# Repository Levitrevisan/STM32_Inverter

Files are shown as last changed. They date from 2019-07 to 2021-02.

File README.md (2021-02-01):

# STM32 Inverter
## Introduction:

University project: Simple micro-inverter using a STM32F103C8.

## Objectives

Generate 3 phase signal through SPWM with 120 degrees of phase diffence. The frequency, phase and amplitude should be controlled through digital buttons.

## Project Roadmap

*  [OK] Be able to generate 6 PWM pulses with different duty cycles
*  [OK] Be able to control duty cycles inside timmed interruption routines
*  [OK] Guarantee that interruption have the timer and counter well adjusted to required time.
*  [OK] Be able to generate 3 SPWM waves with 120 between them
*  [OK] Guarantee that SPWM generated have 120 degrees between them
*  [OK] Control SPWM Amplitude
*  [OK] Implement GPIO input interruption
*  [--] Read Zero Cross signal
*  [OK] Control phase based on Zero Cross signal

## Reference

*  https://www.infineon.com/dgdl/Infineon-IM393-S6E-DS-v02_00-EN.pdf?fileId=5546d462696dbf1201699a9d912478e4 - INFINEON CIPOS datasheet
*  https://www.infineon.com/dgdl/Infineon-AN2016-11_CIPOS_Mini_Inverter_module_reference_board_type1_for_1-shunt_resistor-AN-v01_11-EN.pdf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 - Evaluation board manual (used for "benchmarking" propuses)
*  https://www.st.com/content/ccc/resource/technical/document/reference_manual/59/b9/ba/7f/11/af/43/d5/CD00171190.pdf/files/CD00171190.pdf/jcr:content/translations/en.C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 - STM32 reference manual

## How to use MatLab script to generate SPWM values

The matlab script is used to generate the senoid values that are used as reference for the SPWM generation. You should se the parameters

```
  max_pwm_value = 3550;
  min_pwm_value = 0;
  frequency = 60;
  number_of_points_in_one_cycle = 60;
```

The script will return the int array to be pasted into the MCU code like this:

```
  {1775 ,1961 ,2144 ,2324 ,2497 ,2663 ,2818 ,2963 ,3094 ,3211 ,3312 ,3397 ,3463 ,3511 ,3540 ,3550 ,3540 ,3511 ,3463 ,3397 ,3312 ,3211 ,3094 ,2963 ,2818 ,2663 ,2497 ,2324 ,2144 ,1961 ,1775 ,1589 ,1406 ,1226 ,1053 ,888 ,732 ,587 ,456 ,339 ,238 ,153 ,87 ,39 ,10 ,0 ,10 ,39 ,87 ,153 ,238 ,339 ,456 ,587 ,732 ,887 ,1053 ,1226 ,1406 ,1589 ,}
```
  
It will also return the interuption period in nanoseconds used to control the timed interruption that will update the PWM values to generate the senoid. Lastly, it will show us the stem plot of those points.

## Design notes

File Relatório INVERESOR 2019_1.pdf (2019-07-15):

UNIVERSIDADE FEDERAL DO RIO GRANDE DO SUL- UFRGS ESCOLA DE ENGENHARIA - DEPARTAMENTO DE ENGENHARIA ELÉTRICA
APLICAÇÕES INDUSTRIAIS DA ELETRÔNICA

### Levi Trevisan Gustavo C. Casara Pedro Henrique Dal Pizzol

### Projeto Final da Disciplina de Aplicações Industriais da Eletrônica:

### Implementação de um inversor trifásico para adaptação da geração

fotovoltaica à rede.

Porto Alegre, 2019

Resumo

O projeto desenvolvido teve como objetivo implementar um inversor trifásico que permite que a energia gerada a partir de uma planta solar (tensão DC) possa ser injetada na rede.
A partir de uma série de PWMs modulados senoidalmente, conseguimos utilizar o chip IM393-S6E da INFINEON de maneira semelhante a um driver, usando como fonte a tensão DC de alta potência.
O projeto é separado entre parte de controle e parte de potência, elas têm isolamento galvânico entre si a partir de optoacopladores, em momento nenhum o nível de 3.3V do microprocessador estará exposto diretamente a parte de potência.
Utilizando um filtro do tipo passa-baixa na saída trifásica do projeto, pode-se observar uma saída trifásica com três senóides defasadas em 120º. Também foi projetado um filtro LCL para ser utilizado após o inversor.

1- Alimentações

1.1 - Microprocessador

O microprocessador utilizado foi o BluePill STM32. Nele há um regulador 3.3V de forma que qualquer alimentação entre 5V e 3.3V é suficiente para utilizá-lo.
Foi escolhida então uma fonte comum de celular 5V e 1A, pois já é compatível com a entrada USB mostrada na Figura 1

Figura 1 - BluePill STM32

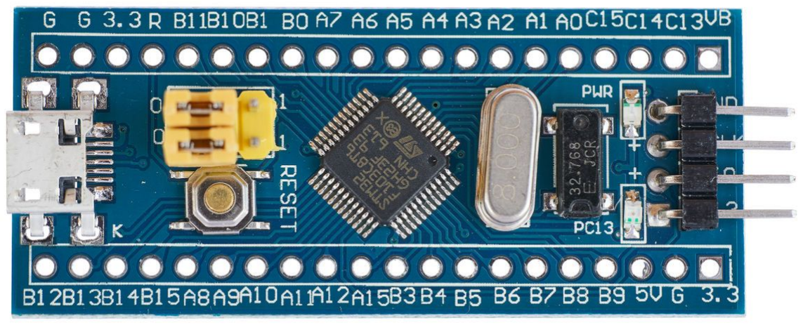
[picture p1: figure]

1.2 - IM393-S6E INFINEON

Para a alimentação do chip da INFINEON foi utilizada uma fonte de 15V 1,6A, que será conectada na rede para alimentar o chip e o regulador de 3.3V que será abordado a seguir.

### 1.3 Regulador 3.3V (parte de Potência)

Para alimentar o “secundário” dos optoacopladores com uma fonte isolada da parte de controle, aproveitamos os 15V que alimentam o INFINEON. A partir de um regulador LM317 ajustável, utilizamos um trimpot para ajuste fino da tensão que deve ser 3.3V.

Figura 2 - Esquemático do regulador de tensão de 3.3V

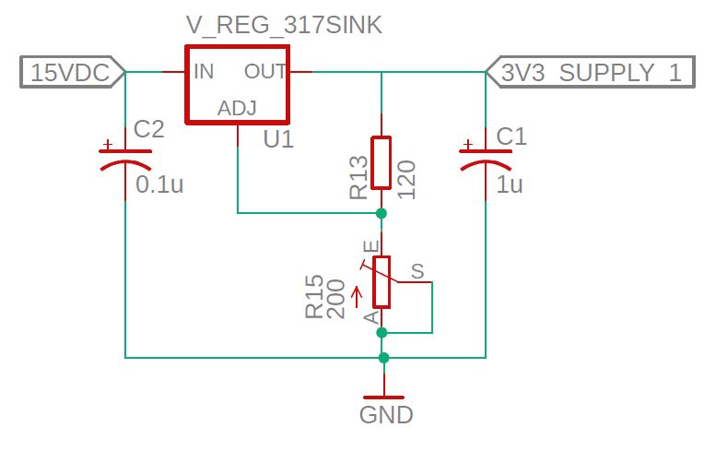
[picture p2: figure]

2- Controle

O controle da amplitude e da frequência do sinal de saída do inversor são feitos através de sinais PWM. Controlando a largura de cada pulso conseguimos, em média, diferentes níveis de tensão, da mesma forma, variando a média do sinal varia-se a frequência.
Para gerar os sinais PWM, que controlam cada um dos seis semi-ciclos (um semi-ciclo positivo e negativo para cada uma das três fases) foram utilizadas as portas PWM do microprocessador BluePill STM32, seus timers e funções de interrupção.
Foi definido que o sinal teria sessenta diferentes níveis de tensão, níveis estes, que seriam aplicados em sequência na saída, gerando uma senóide com “degraus”.
Para atender esta definição as interrupções foram definidas para ocorrerem a cada 277,77778µs e, assim, atualizar o valor do PWM para o valor seguinte.
Para o microprocessador utilizado temos que o valor máximo do sinal PWM é de 3550, para este valor o nível lógico da saída fica alto por do 100% do duty cicle. E para o valor zero o nível lógico fica baixo para todo o duty cicle.
Dividindo um período da senóide em 60 amostras, foi feito um vetor que apresenta os valores que devem ser utilizados para controlar o duty cicle do PWM.

senoid_pwm = [1775 ,1961 ,2144 ,2324 ,2497 ,2663 ,2818 ,2963 ,3094 ,3211 ,3312 ,3397 ,3463 ,3511 ,3540 ,3550 ,3540 ,3511 ,3463 ,3397 ,3312 ,3211 ,3094 ,2963 ,2818 ,2663 ,2497 ,2324 ,2144 ,1961 ,1775 ,1589 ,1406 ,1226 ,1053 ,888 ,732 ,587 ,456 ,339 ,238 ,153 ,87 ,39 ,10 ,0 ,10 ,39 ,87 ,153 ,238 ,339 ,456 ,587 ,732 ,887 ,1053 ,1226 ,1406 ,1589]

Plotando o vetor acima obtemos o seguinte gráfico:

Figura 3 - Plot com os gráficos de valores utilizados na função PWM do microprocessador.

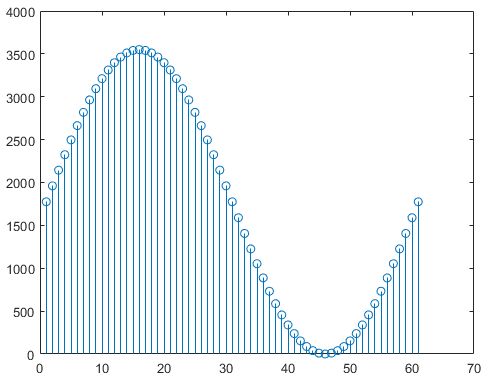
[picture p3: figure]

Como pode ser visto na Figura 2, a sequência dos valores do vetor senoid_pwm formam a senóide desejada e necessária para o projeto.
Para conseguir a defasagem de 120° entre as fases, a função PWM deve começar com primeira posição do vetor para a fase R, com a vigésima posição para a fase S e com a quadragésima posição para a fase T.

3- Isolamento Galvânico

O isolamento galvânico consiste em ter dois sistemas elétricos com terras diferentes que se comuniquem sem o fluxo de correntes indesejadas.
A isolação galvânica é importante para fins de segurança, de forma que um usuário que tenha acesso a botões ou ao microprocessador nunca entre em contato com a parte de potência e também é importante para fins de proteção, pois se houver algum problema com o circuito de potência o mesmo não afetará a parte de controle.
Para obter tal isolação, são utilizados optoacopladores. Foram feitos testes iniciais com os modelos 4N25 e PC817, porém nenhum deles demonstrou uma resposta satisfatória na frequência de 20kHz que o nosso PWM opera.
Optou-se então por utilizar um optoacoplador de alta velocidade. O modelo que encontramos em Porto Alegre para comprar foi 6N135. Quando este optoacoplador recebe o PWM na entrada do seu LED emissor interno diretamente do microprocessador ele inverte a saída, optamos por utilizar uma topologia alternativa mostrada na figura abaixo, nela temos dois ganhos, o microprocessador não precisa fornecer a corrente do PWM (um microprocessador sempre suporta receber mais corrente do que fornecer) e a saída do optoacoplador é a mesma que o PWM gerado no microprocessador.

Figura 4 - Topologia do 6N135

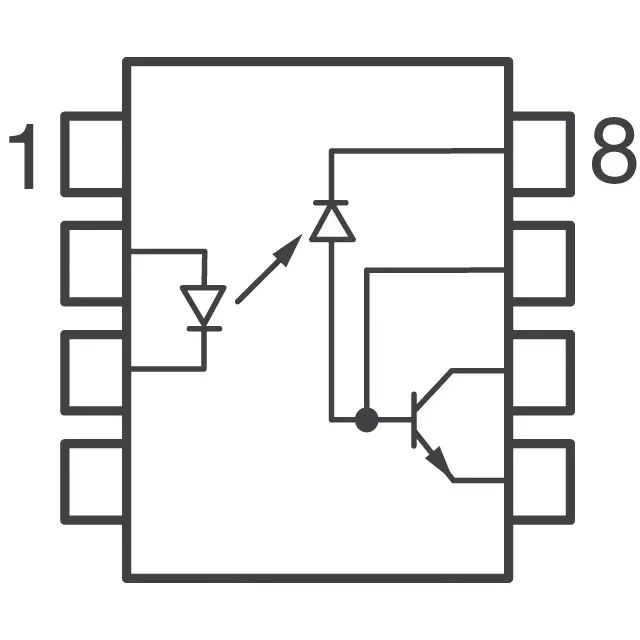
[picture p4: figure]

Figura 5 - Esquemático do isolamento galvânico através de optoacopladores

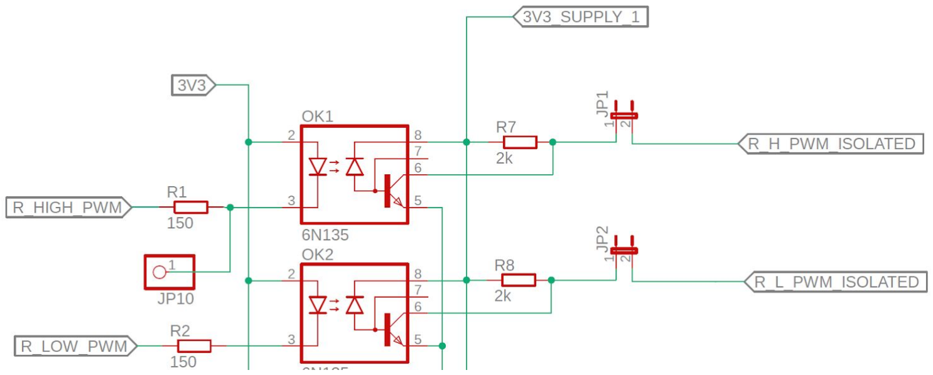
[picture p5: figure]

Podemos ver no lado “primário” do optoacoplador os PWMs do High Input e do Low Input do INFINEON. Os resistores R1 e R2 foram projetados para que haja uma corrente grande suficiente para que os LEDs emitam o sinal com a intensidade necessária.
Já no lado “secundário” há um resistor recomendado no datasheet do 6N135 e jumpers para fins de testes do circuito.

4- INFINEON

Caracterizamos como a parte de potência o nosso chip da INFINEON e o que envolve a tensão de 300V.
A tag “High DC in” é a entrada de 300V. Ela é conectada ao pino V+ do INFINEON. As alimentações de 15V vão nos pinos de VDD do chip. Adicionalmente, ambas referências (da fonte de 15V quando da fonte de 300V) irão no pino de COM do INFINEON.
Todos os pinos de Hin e Lin estão diretamente ligados nos “secundários” dos optoacopladores.
Também foram inseridos capacitores de bootstrap entre os pinos da saída Vs e os pinos de Vb, conforme indicado tanto no datasheet do chip quando em manuais de aplicação indicados pelo Professor.

Figura 6 - Esquemático utilizado para as ligações do INFINEON

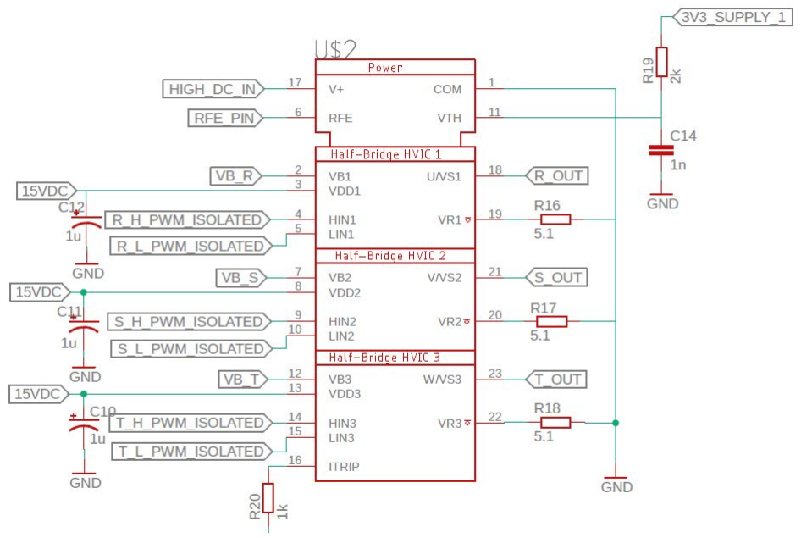
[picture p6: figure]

Figura 7 - Capacitores de BootsTrap entre a Vs e Vb

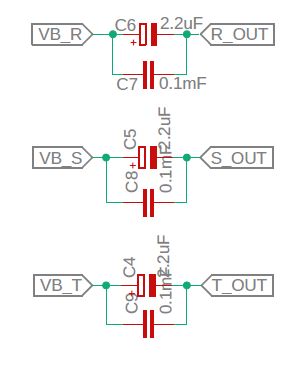
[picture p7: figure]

5- Detector de Passagem por zero

O detector de passagem por zero é o circuito capaz de detectar quando a tensão da rede AC passa de uma tensão negativa para positiva e vice-versa. Essa informação é útil em retificadores trifásicos grid-tie. Essa informação será utilizada pelo microprocessador para ajustar as fases deixando-as sincronizadas com a rede, ou levemente adiantada para que a energia flua dos painéis solares para a rede.
O led do optoacoplador conduzirá em apenas metade do período, o período positivo, assim obtém-se um sinal digital que indica quando a fase está no ciclo positivo e quando não está.

O resistor de 100KΩ limita a corrente evitando queimar o led. O diodo em paralelo com o optoacoplador serve para evitar a tensão reversa sobre o led.
Além do optoacoplador fornecer um sinal digital de interesse ele também serve de isolamento galvânico para o microprocessador.

Figura 8 - Esquemático do detector de zero.

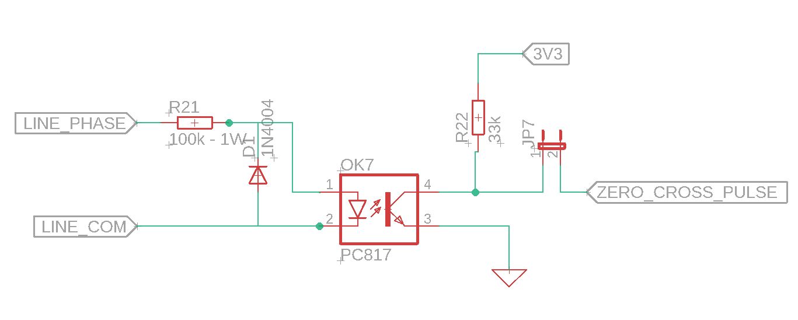
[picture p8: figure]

6- Filtro de saída

Para o filtro de saída de testes, foi utilizado um filtro RC passa-baixa. Utilizamos como frequência de corte 120Hz no teste.
O capacitor utilizado foi de 22uF e a resistência de 60Ω.

Figura 9 - Filtro passa-baixa RC.

Foi pedido também no projeto o dimensionamento de um filtro LCL. Foi utilizado como referência a dissertação de mestrado de Rômulo Diniz Araujo
(http://www.gpec.ufc.br/novasdissertacoes/13.pdf) e também as notas de aula do Prof. Heverton Augusto Pereira da UFV (http://www.gesep.ufv.br/wp-content/uploads/Aula_06-Conversores-cc_ca-Filtro-LCL.pdf).

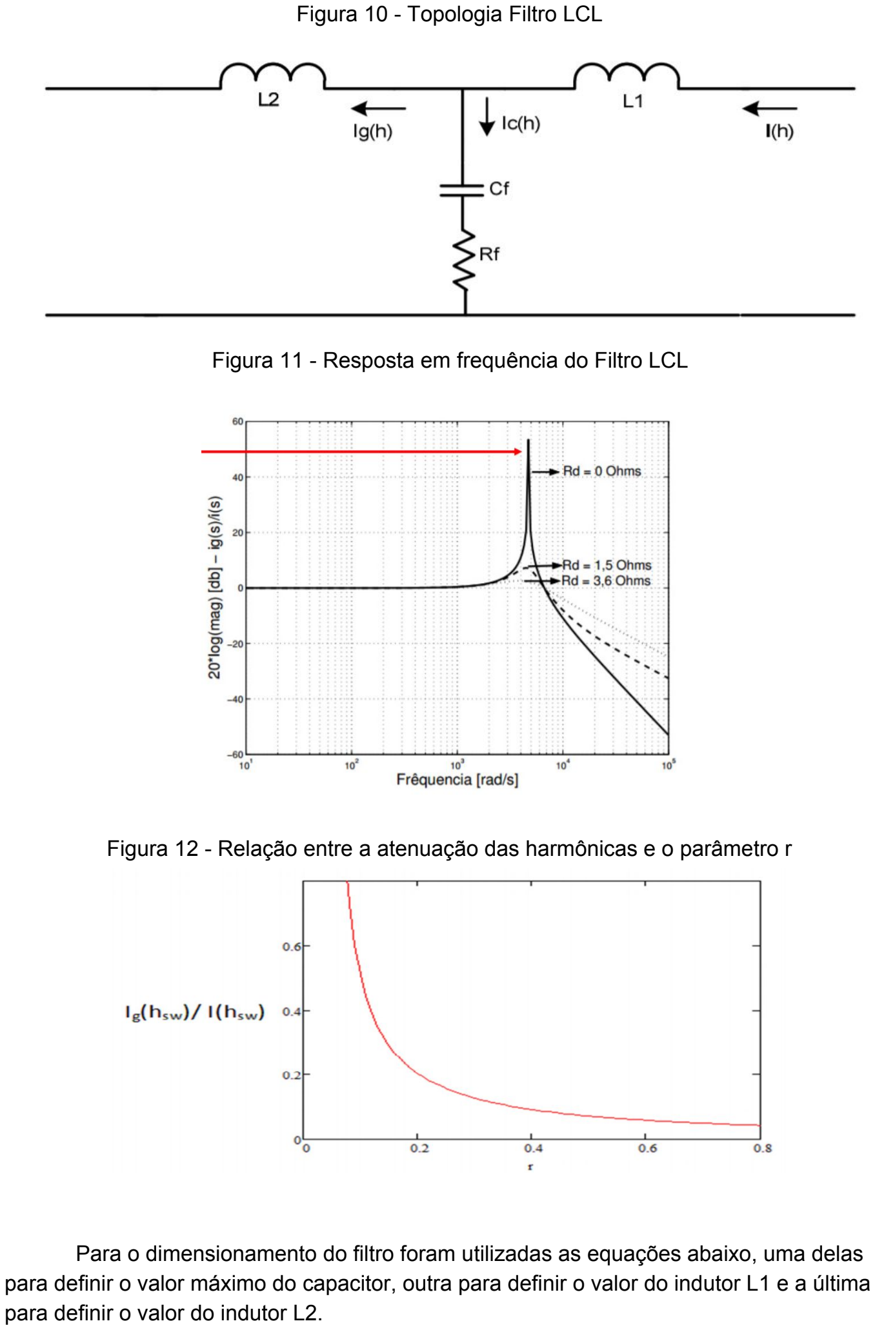
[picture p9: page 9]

Figura 10 - Topologia Filtro LCL

Figura 11 - Resposta em frequência do Filtro LCL

Figura 12 - Relação entre a atenuação das harmônicas e o parâmetro r

Para o dimensionamento do filtro foram utilizadas as equações abaixo, uma delas para definir o valor máximo do capacitor, outra para definir o valor do indutor L1 e a última para definir o valor do indutor L2.

O valor da capacitância máxima é representado na equação abaixo, ela é definida para que o fator de potência do filtro se mantenha alto, quanto maior a capacitância utilizada menor será o indutor necessário.
Foi utilizada como a nossa tensão de saída a tensão de linha da rede, a corrente máxima como 6A e frequência de chaveamento de 20kHz. No artigo, Rômulo Araujo utilizou como % de ripple na corrente 31% e o fator r como 20%, seguimos estas definições para o dimensionamento.

Os valores do dimensionamento estão no quadro abaixo.

L1 [mH] | L2 [mH] | Cf [nF] | Rf [Ω]
7,2 | 1,44 | 60 | 3,6

7 - Roteiro de Testes

Para um correto uso do inversor deve-se seguir os seguintes passos:

1. Ainda com o circuito desligado, deve-se retirar todos os 6 jumpers presentes na placa. Para impedir que qualquer qualquer sinal chegue em chip da INFINEON.
2. Alimentar o microprocessador com a fonte de 5V e verificar se ele está gerando os sinais PWM.
3. Alimentar o circuito com a fonte de 15V. Os 15V alimentam o regulador de tensão que alimenta os optoacopladores e demais circuitos relevantes.
4. Verificar se o regulador de tensão, agora alimentado com 15V, possui 3,3V na sua saída. Não sendo verdadeiro a tensão de saída pode ser regulada ajustando o trimpot.
5. Com o passo 4 atendido verifica-se as saídas dos optoacopladores. Neles devem ser observados os mesmos sinais PWM observados no passo 2.
6. Ligar uma das fases ao detector de passagem por zero. Verificar se existem pulsos na sua saída.
7. Verificar se o chip da INFINEON está alimentado com 15V nos pinos 3, 8 e 13.
8. Ligar a fonte de 300V.
9. Ler as saídas. O sinal deve ser parecido ao dos ítens 2 e 5.
10. Conectar o filtro a saída trifásica.
11. Ler as saídas depois de passarem pelo filtro.

Figura 13 - Saída do inversor após o filtro RC (fonte DC de 22,5V como alimentação)

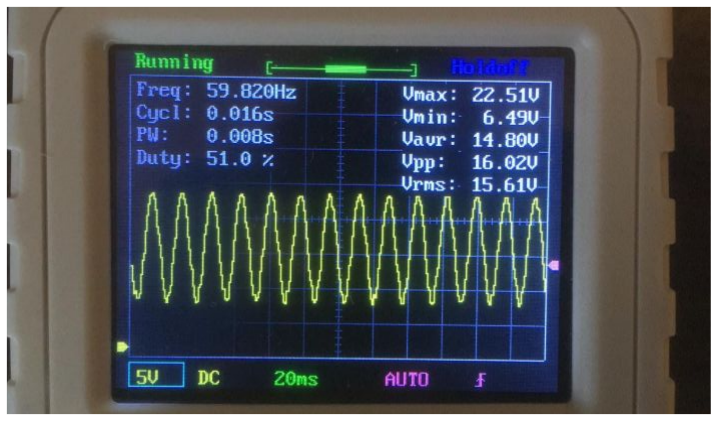
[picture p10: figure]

Figura 14- PWM na entrada do INFINEON (pelas limitações do osciloscópio só conseguimos congelar a parte de duty cycle baixo)

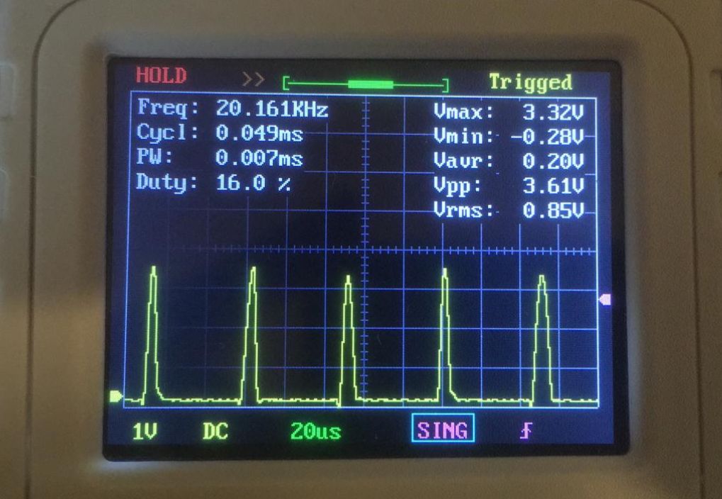
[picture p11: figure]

Figura 14- PWM na saída do INFINEON com 24V CC.

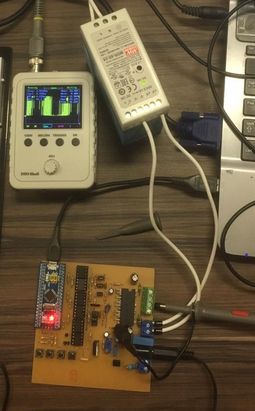
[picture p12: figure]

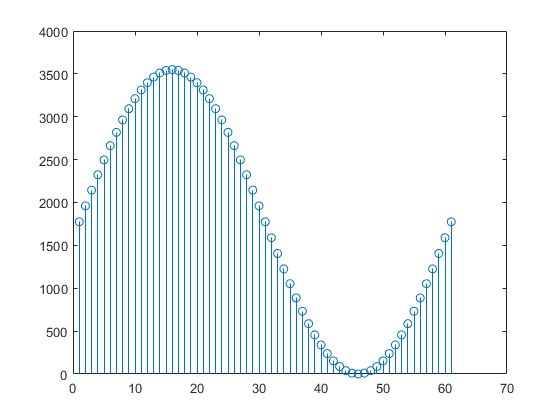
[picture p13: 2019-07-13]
senoid_generator_matlab/untitled.png

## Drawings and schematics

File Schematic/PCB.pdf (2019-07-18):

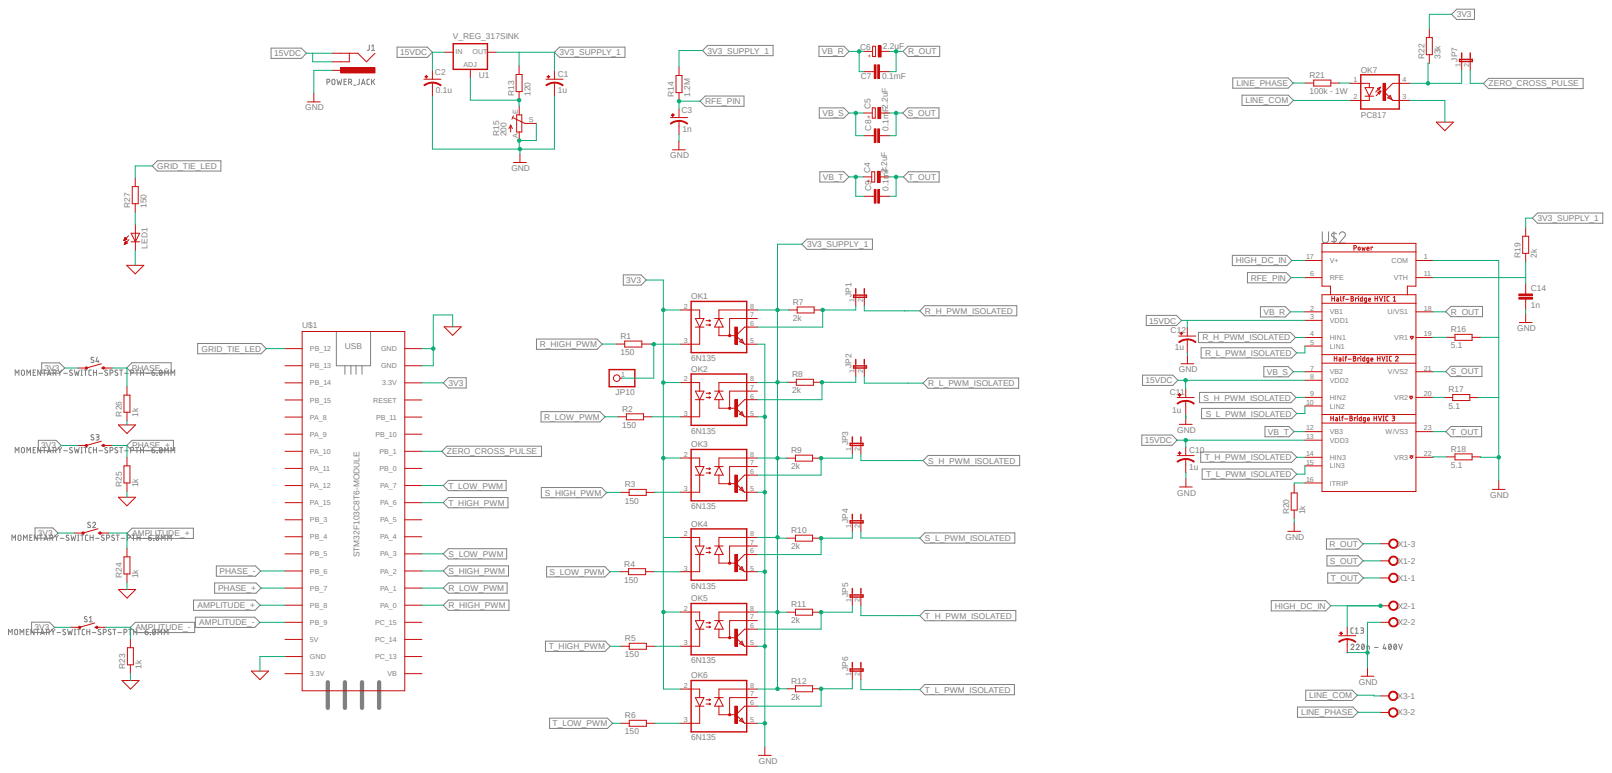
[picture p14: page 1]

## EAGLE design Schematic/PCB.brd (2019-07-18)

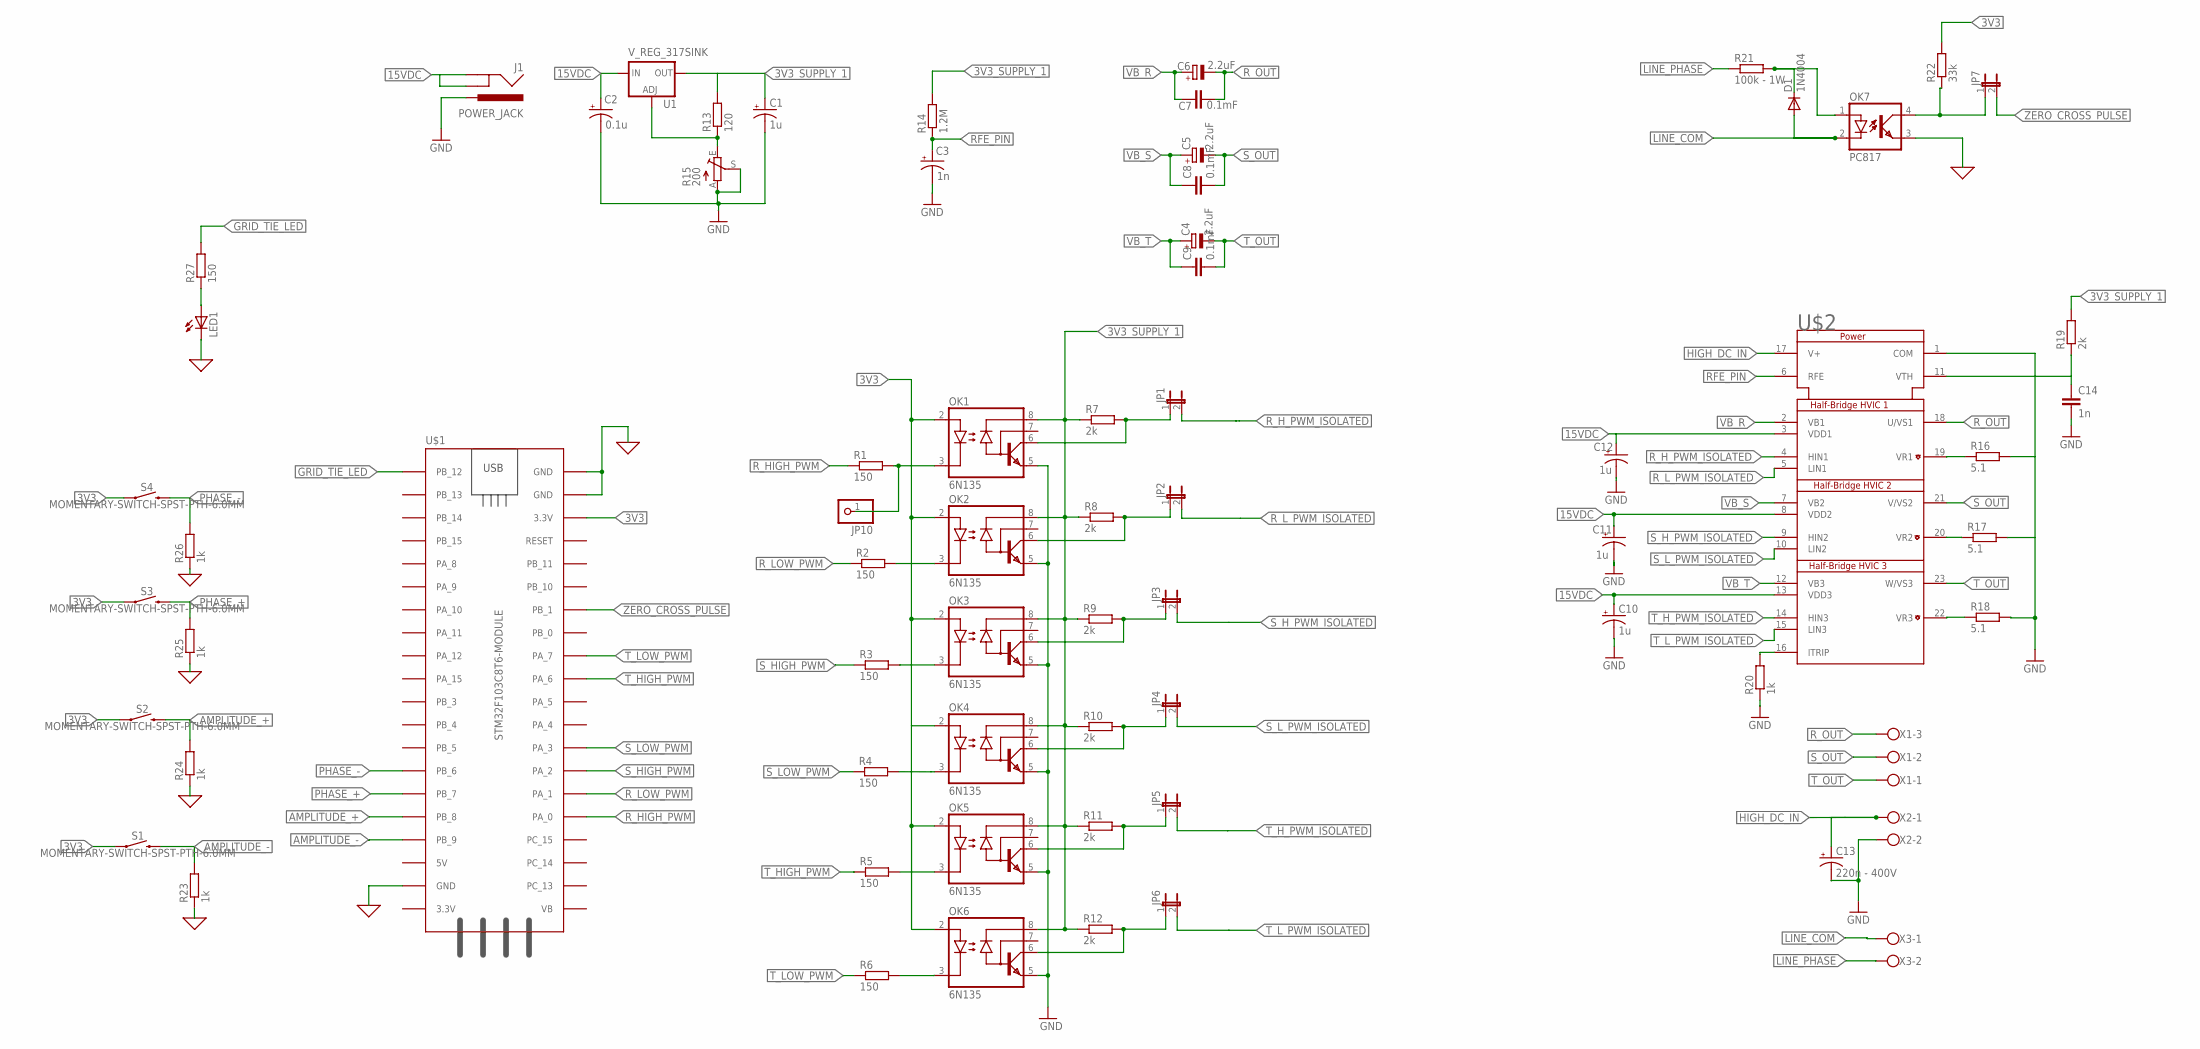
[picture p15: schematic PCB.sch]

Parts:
C1, C10, C11, C12: 1u; E5-4
C2: 0.1u; E5-4
C3: 1n; E5-4
C4, C5, C6: 2.2uF; E3,5-8
C7, C8, C9: 0.1mF; C5B5
C13: 220n - 400V; CPOL-RADIAL-5MM-10MM-KIT
C14: 1n; C5B2.5
D1: 1N4004; DO41-10
J1: POWER_JACK; POWER_JACK_PTH
JP1, JP2, JP3, JP4, JP5, JP6, JP7: JP1E; JP1
JP10: PINHD-1X1; 1X01
LED1: LED3MM
OK1, OK2, OK3, OK4, OK5, OK6: 6N135; DIL08
OK7: PC817; DIL04
R1, R2, R3, R4, R5, R6, R27: 150; 0207/10
R7, R8, R9, R10, R11, R12, R19: 2k; 0207/10
R13: 120; 0207/10
R14: 1.2M; 0207/10
R15: 200; RJ9W
R16, R17, R18: 5.1; 0207/10
R20, R23, R24, R25, R26: 1k; 0207/10
R21: 100k - 1W; 0207/10
R22: 33k; 0207/10
S1, S2, S3, S4: MOMENTARY-SWITCH-SPST-PTH-6.0MM; TACTILE_SWITCH_PTH_6.0MM
U1: V_REG_317SINK; TO220-ADJ
U$1: STM32F103C8T6-MODULE
U$2: IM231-M6T2B; DIP-IM231-M6T2B
X1: W237-103
X2, X3: W237-102

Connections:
0: LED1.K (C), OK7.3 (EMIT), R23.1, R24.1, R25.1, R26.1, U$1.GND_1 (GND), U$1.GND_2 (GND), U$1.GND_3 (GND)
3V3: OK1.2 (A), OK2.2 (A), OK3.2 (A), OK4.2 (A), OK5.2 (A), OK6.2 (A), R22.2, S1.1, S2.1, S3.1, S4.1, U$1.3.3V_2 (3.3V)
3V3_SUPPLY_1: C1.+, OK1.8 (VCC), OK2.8 (VCC), OK3.8 (VCC), OK4.8 (VCC), OK5.8 (VCC), OK6.8 (VCC), R7.1, R8.1, R9.1, R10.1, R11.1, R12.1, R13.2, R14.2, R19.2, U1.OUT
15VDC: C2.+, C10.+, C11.+, C12.+, J1.GND, J1.GNDBREAK, U1.IN, U$2.3 (VDD1), U$2.8 (VDD2), U$2.13 (VDD3)
AMPLITUDE_+: R24.2, S2.3 (2), U$1.PB_8
AMPLITUDE_-: R23.2, S1.3 (2), U$1.PB_9
GND: C1.-, C2.-, C3.-, C10.-, C11.-, C12.-, C13.-, C14.2, J1.PWR, OK1.5 (GND), OK2.5 (GND), OK3.5 (GND), OK4.5 (GND), OK5.5 (GND), OK6.5 (GND), R15.A, R15.S, R16.2, R17.2, R18.2, R20.1, U$2.1 (COM), X2.2
GRID_TIE_LED: R27.2, U$1.PB_12
HIGH_DC_IN: C13.+, U$2.17 (V+), X2.1
LINE_COM: D1.A, OK7.2 (C), X3.1
LINE_PHASE: R21.1, X3.2
unnamed: JP10.1, OK1.3 (C), R1.2
unnamed: OK2.3 (C), R2.2
unnamed: OK3.3 (C), R3.2
unnamed: OK4.3 (C), R4.2
unnamed: OK5.3 (C), R5.2
unnamed: OK6.3 (C), R6.2
unnamed: R13.1, R15.E, U1.ADJ
unnamed: R20.2, U$2.16 (ITRIP)
unnamed: R16.1, U$2.19 (VR1)
unnamed: R17.1, U$2.20 (VR2)
unnamed: R18.1, U$2.22 (VR3)
unnamed: D1.C, OK7.1 (A), R21.2
unnamed: C14.1, R19.1, U$2.11 (VTH)
unnamed: JP7.1, OK7.4 (COL), R22.1
unnamed: LED1.A, R27.1
PHASE_+: R25.2, S3.3 (2), U$1.PB_7
PHASE_-: R26.2, S4.3 (2), U$1.PB_6
RFE_PIN: C3.+, R14.1, U$2.6 (RFE)
R_HIGH_PWM: R1.1, U$1.PA_0
R_HIGH_PWM_ISOLATED: JP1.1, OK1.6 (VO), R7.2
R_H_PWM_ISOLATED: JP1.2, U$2.4 (HIN1)
R_LOW_PWM: R2.1, U$1.PA_1
R_LOW_PWM_ISOLATED: JP2.1, OK2.6 (VO), R8.2
R_L_PWM_ISOLATED: JP2.2, U$2.5 (LIN1)
R_OUT: C6.-, C7.2, U$2.18 (U/VS1), X1.3
S_HIGH_PWM: R3.1, U$1.PA_2
S_HIGH_PWM_ISOLATED: JP3.1, OK3.6 (VO), R9.2
S_H_PWM_ISOLATED: JP3.2, U$2.9 (HIN2)
S_LOW_PWM: R4.1, U$1.PA_3
S_LOW_PWM_ISOLATED: JP4.1, OK4.6 (VO), R10.2
S_L_PWM_ISOLATED: JP4.2, U$2.10 (LIN2)
S_OUT: C5.-, C8.2, U$2.21 (V/VS2), X1.2
T_HIGH_PWM: R5.1, U$1.PA_6
T_HIGH_PWM_ISOLATED: JP5.1, OK5.6 (VO), R11.2
T_H_PWM_ISOLATED: JP5.2, U$2.14 (HIN3)
T_LOW_PWM: R6.1, U$1.PA_7
T_LOW_PWM_ISOLATED: JP6.1, OK6.6 (VO), R12.2
T_L_PWM_ISOLATED: JP6.2, U$2.15 (LIN3)
T_OUT: C4.-, C9.2, U$2.23 (W/VS3), X1.1
VB_R: C6.+, C7.1, U$2.2 (VB1)
VB_S: C5.+, C8.1, U$2.7 (VB2)
VB_T: C4.+, C9.1, U$2.12 (VB3)
ZERO_CROSS_PULSE: JP7.2, U$1.PB_1

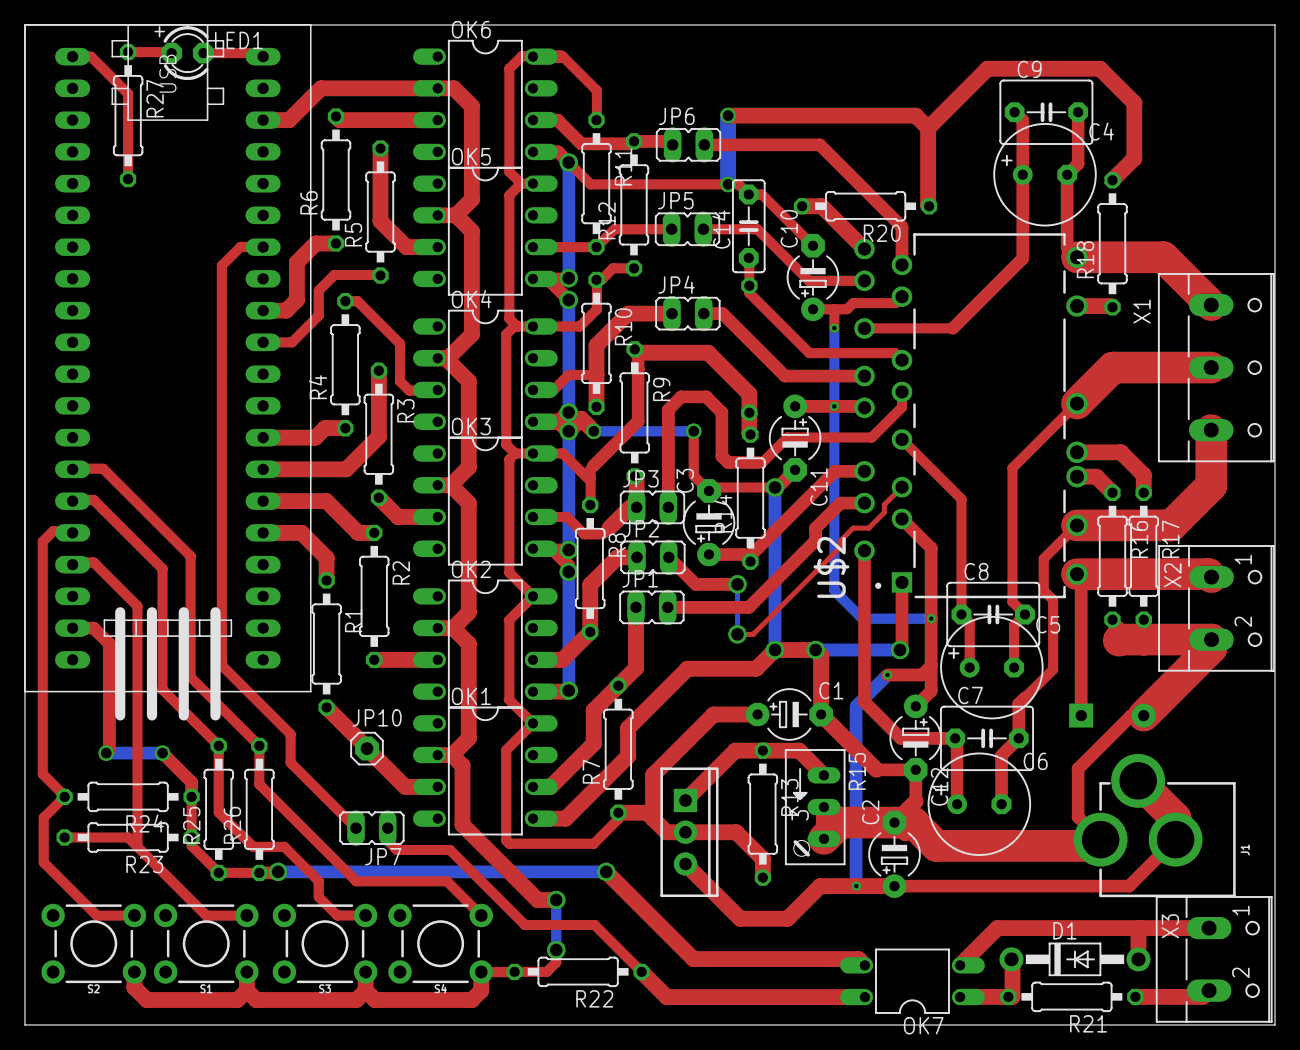
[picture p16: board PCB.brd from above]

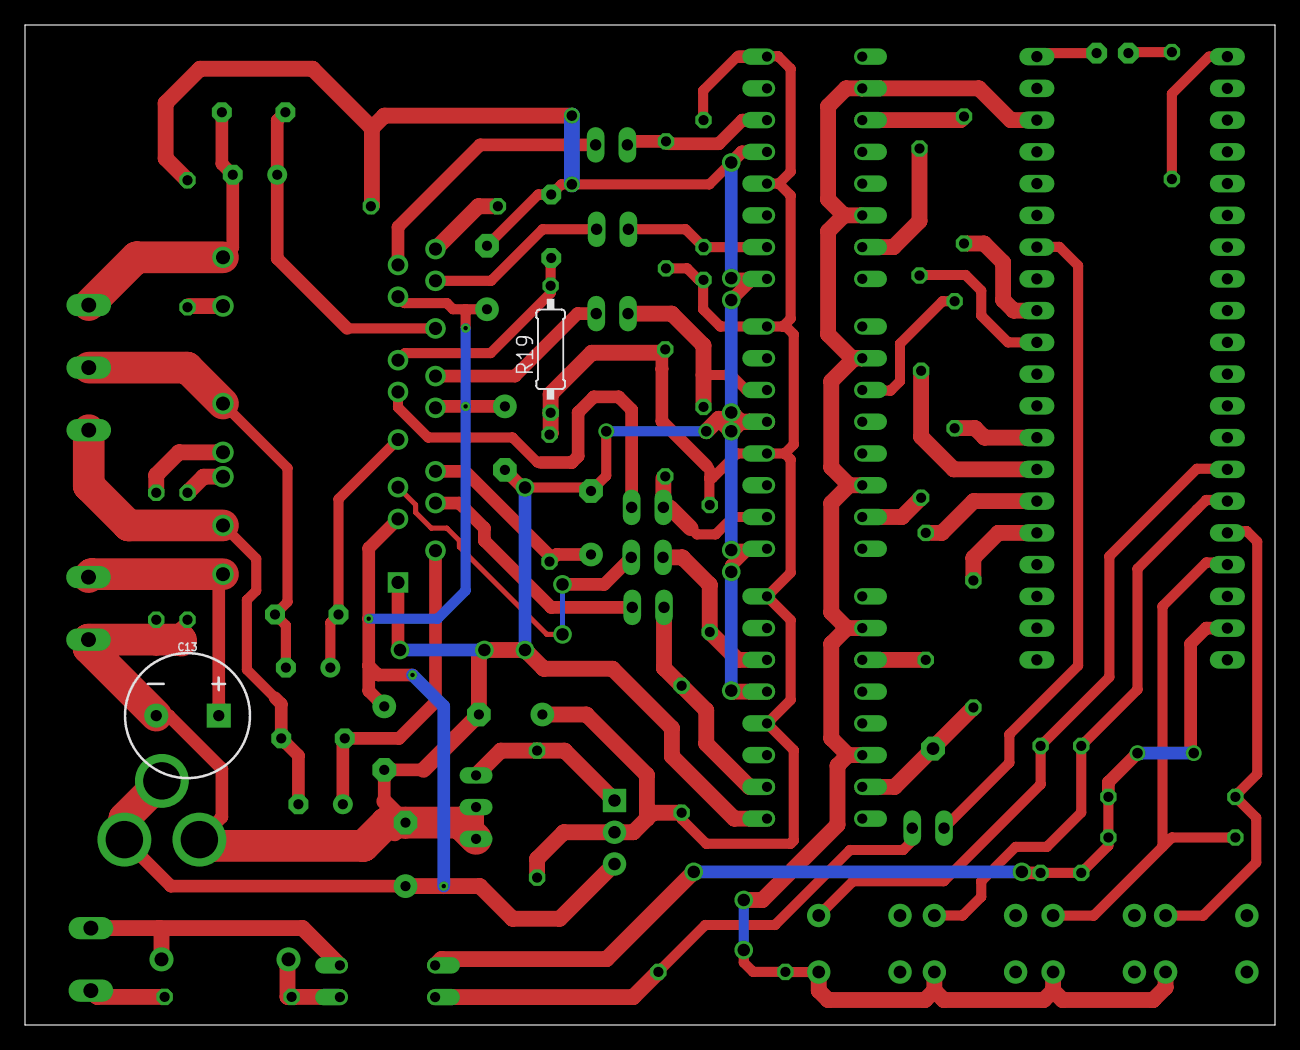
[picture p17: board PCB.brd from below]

Board: 2 copper layers, 100.0 x 80.0 mm, 69 parts (2 on the bottom side), 54 nets.

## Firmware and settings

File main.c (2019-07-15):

#include "stm32f10x.h"
#include "stm32f10x_gpio.h"
#include "stm32f10x_exti.h"
#include "stm32f10x_conf.h"
#include "stm32f10x_tim.h"

/*
Connections map:
Interface Buttons:
PB6 - "Phase -" button
PB7 - "Phase +" button
PB8 - "Amplitude +" button
PB9 - "Amplitude -" button
*/


#define PWM_TIMERS_PRESCALER 0	
#define PWM_TIMERS_PERIOD 3550
#define PWM_TIMERS_INIT_PULSE 500
#define NUMBER_OF_POINTS_IN_ONE_CYCLE 60

// Senoid Pattern generated in MatLab Script on subfolder

int senoid_pwm[NUMBER_OF_POINTS_IN_ONE_CYCLE] = {1775 ,1961 ,2144 ,2324 ,2497 ,2663 ,2818 ,2963 ,3094 ,3211 ,3312 ,3397 ,3463 ,3511 ,3540 ,3550 ,3540 ,3511 ,3463 ,3397 ,3312 ,3211 ,3094 ,2963 ,2818 ,2663 ,2497 ,2324 ,2144 ,1961 ,1775 ,1589 ,1406 ,1226 ,1053 ,888 ,732 ,587 ,456 ,339 ,238 ,153 ,87 ,39 ,10 ,0 ,10 ,39 ,87 ,153 ,238 ,339 ,456 ,587 ,732 ,887 ,1053 ,1226 ,1406 ,1589};

// State Control Variables

int t_senoid_R_init_value = 0;
int t_senoid_S_init_value = NUMBER_OF_POINTS_IN_ONE_CYCLE/3;
int t_senoid_T_init_value = NUMBER_OF_POINTS_IN_ONE_CYCLE*2/3;
	
int t_senoid_R = 0;
int t_senoid_S = NUMBER_OF_POINTS_IN_ONE_CYCLE/3;
int t_senoid_T = NUMBER_OF_POINTS_IN_ONE_CYCLE*2/3;
	
float amplitudeFactor = 0.8;
	
int isGridTie = 0;

// Functions Prototypes										

void debounceDelay(unsigned int nCount);
void InitializeTimer2(void);
void InitializeTimer3(void);
void InitializeTimer4IT(void);
void InitializeGPIOInterruptionOnPB6(void);
void InitializePWMChannels(void);
void InitializePWMGPIO(void);
void InitializeLEDGPIO(void);
void InitializeButtonsGPIO(void);
void toggle_led_PC13(void);
void changeRpositiveDutyCycle(int dutyCycle);
void changeRnegativeDutyCycle(int dutyCycle);
void changeSpositiveDutyCycle(int dutyCycle);
void changeSnegativeDutyCycle(int dutyCycle);
void changeTpositiveDutyCycle(int dutyCycle);
void changeTnegativeDutyCycle(int dutyCycle);
void updatePhaseR(void);
void updatePhaseS(void);
void updatePhaseT(void);
void incrementSenoidPosition(void);
void decrementSenoidPosition(void);
void buttonPressDetection(void);

void setup(){
	InitializeLEDGPIO();
	InitializeTimer2();
	InitializeTimer3();
	InitializePWMChannels();
	InitializePWMGPIO();
	InitializeGPIOInterruptionOnPB6();
	InitializeTimer4IT();
}


int main(){
	
	setup();
	
	while(1){
		
		buttonPressDetection();
		
	}
	

return 0;
}

void incrementSenoidPosition(){
		if ((t_senoid_R < 60) & (t_senoid_S < 60) & (t_senoid_T < 60)){
			t_senoid_R ++;
			t_senoid_S ++;
			t_senoid_T ++;
		}
}

void decrementSenoidPosition(){
	if ((t_senoid_R > 0) & (t_senoid_S > 0) & (t_senoid_T > 0)){
		t_senoid_R --;
		t_senoid_S --;
		t_senoid_T --;
	}
}
	
void buttonPressDetection(){
				
	if (GPIO_ReadInputDataBit(GPIOB, GPIO_Pin_6) | GPIO_ReadInputDataBit(GPIOB, GPIO_Pin_7) | GPIO_ReadInputDataBit(GPIOB, GPIO_Pin_8) | GPIO_ReadInputDataBit(GPIOB, GPIO_Pin_9)){
		debounceDelay(100);	
		//detect 2 buttons long press
		if (GPIO_ReadInputDataBit(GPIOB, GPIO_Pin_6) & GPIO_ReadInputDataBit(GPIOB, GPIO_Pin_8)){
			toggle_led_PC13();
			if (isGridTie == 1){
				isGridTie = 0;
			} else {
				isGridTie = 1;
			}
		} else if (GPIO_ReadInputDataBit(GPIOB, GPIO_Pin_6)){
			/*Phase -*/
			decrementSenoidPosition();
		} else if(GPIO_ReadInputDataBit(GPIOB, GPIO_Pin_7)){
			/*Phase +*/
			incrementSenoidPosition();
		} else if(GPIO_ReadInputDataBit(GPIOB, GPIO_Pin_8)){
			/*Amplitude -*/			
			//avoid negative amplitudes
				if (!(amplitudeFactor <= 0)){
					amplitudeFactor = amplitudeFactor - 0.05;
				}
		} else if(GPIO_ReadInputDataBit(GPIOB, GPIO_Pin_9)){
			/*Amplitude +*/
			// avoid sinewave distortions
			if (!(amplitudeFactor >= 1)){
				amplitudeFactor = amplitudeFactor + 0.05;
			}
		}
		
		// avoid double press
		debounceDelay(200);	
	}

}

void InitializeLEDGPIO(){
	// Enable clock for GPIOC
	RCC_APB2PeriphClockCmd(RCC_APB2Periph_GPIOC, ENABLE);

	GPIO_InitTypeDef GPIO_InitStructure;
	//GPIO_StructInit(&GPIO_InitStructure);
	
	GPIO_InitStructure.GPIO_Pin	= GPIO_Pin_13; //Analog voltages to be measured are connected to pins 1 and 2 of port A, 
	GPIO_InitStructure.GPIO_Speed = GPIO_Speed_2MHz;
	GPIO_InitStructure.GPIO_Mode	= GPIO_Mode_Out_PP; //Output push-pull mode 
	GPIO_Init(GPIOC, &GPIO_InitStructure); // calls the function to actually configure the port A.
	GPIO_SetBits(GPIOC, GPIO_Pin_13);
	
}

void InitializeButtonsGPIO(){

	RCC_APB2PeriphClockCmd(RCC_APB2Periph_GPIOB, ENABLE);

	GPIO_InitTypeDef GPIO_InitStructure;
	GPIO_StructInit(&GPIO_InitStructure);
	GPIO_InitStructure.GPIO_Mode = GPIO_Mode_IN_FLOATING;
	GPIO_InitStructure.GPIO_Speed = GPIO_Speed_2MHz;
	
	GPIO_InitStructure.GPIO_Pin = GPIO_Pin_6;					//PB6
	GPIO_Init(GPIOB , &GPIO_InitStructure);
	GPIO_InitStructure.GPIO_Pin = GPIO_Pin_7;					//PB7
	GPIO_Init(GPIOA , &GPIO_InitStructure);
	GPIO_InitStructure.GPIO_Pin = GPIO_Pin_8;					//PB8
	GPIO_Init(GPIOA , &GPIO_InitStructure);
	GPIO_InitStructure.GPIO_Pin = GPIO_Pin_9;					//PB9
	GPIO_Init(GPIOA , &GPIO_InitStructure);
	
}

void InitializePWMGPIO(){
	// Enable clock for GPIOA
	RCC_APB2PeriphClockCmd(RCC_APB2Periph_GPIOA, ENABLE);

	GPIO_InitTypeDef GPIO_InitStructure;
	GPIO_StructInit(&GPIO_InitStructure);
	GPIO_InitStructure.GPIO_Mode = GPIO_Mode_AF_PP;
	GPIO_InitStructure.GPIO_Speed = GPIO_Speed_2MHz;
	
	GPIO_InitStructure.GPIO_Pin = GPIO_Pin_0;					//PA0
	GPIO_Init(GPIOA , &GPIO_InitStructure);
	GPIO_InitStructure.GPIO_Pin = GPIO_Pin_1;					//PA1
	GPIO_Init(GPIOA , &GPIO_InitStructure);
	GPIO_InitStructure.GPIO_Pin = GPIO_Pin_2;					//PA2
	GPIO_Init(GPIOA , &GPIO_InitStructure);
	GPIO_InitStructure.GPIO_Pin = GPIO_Pin_3;					//PA3
	GPIO_Init(GPIOA , &GPIO_InitStructure);
	GPIO_InitStructure.GPIO_Pin = GPIO_Pin_6;					//PA6
	GPIO_Init(GPIOA , &GPIO_InitStructure);
	GPIO_InitStructure.GPIO_Pin = GPIO_Pin_7;					//PA7
	GPIO_Init(GPIOA , &GPIO_InitStructure);
	
}

void InitializeTimer2(){
	// Enable clock for timer 2
	RCC_APB1PeriphClockCmd(RCC_APB1Periph_TIM2 , ENABLE);
	// Create and initialize TimeBase structure
	TIM_TimeBaseInitTypeDef TIM_TimeBaseStructure;
	TIM_TimeBaseStructInit(&TIM_TimeBaseStructure);
	// Configure TimeBase structure
	TIM_TimeBaseStructure.TIM_Prescaler	= PWM_TIMERS_PRESCALER;//SystemCoreClock/8000 - 1; // considering 8MHz, 1ms
	TIM_TimeBaseStructure.TIM_Period = PWM_TIMERS_PERIOD; // 0..999
	TIM_TimeBaseStructure.TIM_CounterMode = TIM_CounterMode_Up;
	TIM_TimeBaseInit(TIM2, &TIM_TimeBaseStructure);
	TIM_Cmd(TIM2, ENABLE);
	
}

void InitializeTimer3(){
	// Enable clock for timer 2
	RCC_APB1PeriphClockCmd(RCC_APB1Periph_TIM3 , ENABLE);
	// Create and initialize TimeBase structure
	TIM_TimeBaseInitTypeDef TIM_TimeBaseStructure;
	TIM_TimeBaseStructInit(&TIM_TimeBaseStructure);
	// Configure TimeBase structure
	TIM_TimeBaseStructure.TIM_Prescaler	= PWM_TIMERS_PRESCALER;//SystemCoreClock/8 - 1; // considering 8MHz, 1ms
	TIM_TimeBaseStructure.TIM_Period = PWM_TIMERS_PERIOD; // 0..999
	TIM_TimeBaseStructure.TIM_CounterMode = TIM_CounterMode_Up;
	TIM_TimeBaseInit(TIM3, &TIM_TimeBaseStructure);
	TIM_Cmd(TIM3, ENABLE);
	
}

void InitializePWMChannels(){
	
	TIM_OCInitTypeDef TIM_OCInitStructure;
	TIM_OCStructInit(&TIM_OCInitStructure);
	
	// Configuration for the positive parte (non-denied PWM channles)
	TIM_OCInitStructure.TIM_OCMode = TIM_OCMode_PWM2;
	TIM_OCInitStructure.TIM_OutputState = TIM_OutputState_Enable;
	TIM_OCInitStructure.TIM_Pulse = PWM_TIMERS_INIT_PULSE;
	
	//TIM_OCx < X is the PWM channel number
	TIM_OC1Init(TIM2, &TIM_OCInitStructure); //PA0 - R positive
	TIM_OC3Init(TIM2, &TIM_OCInitStructure); //PA2 - S positive
	TIM_OC1Init(TIM3, &TIM_OCInitStructure); //PA6 - T positive
	
	// Configuration for the negative parte (denied PWM channles)
	TIM_OCInitStructure.TIM_OCMode = TIM_OCMode_PWM1;
	
	TIM_OC2Init(TIM2, &TIM_OCInitStructure); //PA1 - R negative
	TIM_OC4Init(TIM2, &TIM_OCInitStructure); //PA3 - S negative
	TIM_OC2Init(TIM3, &TIM_OCInitStructure); //PA7 - T negative
}

void debounceDelay(unsigned int nCount){
		unsigned int i, j;
 
		for (i = 0; i < nCount; i++)
				for (j = 0; j < 0x2AFF; j++);
}

void changeRpositiveDutyCycle(int dutyCycle){
	TIM2->CCR1 = dutyCycle*amplitudeFactor;
}

void changeRnegativeDutyCycle(int dutyCycle){
	TIM2->CCR2 = dutyCycle*amplitudeFactor;
}

void changeSpositiveDutyCycle(int dutyCycle){
	TIM2->CCR3 = dutyCycle*amplitudeFactor;
}

void changeSnegativeDutyCycle(int dutyCycle){
	TIM2->CCR4 = dutyCycle*amplitudeFactor;
}

void changeTpositiveDutyCycle(int dutyCycle){
	TIM3->CCR1 = dutyCycle*amplitudeFactor;
}

void changeTnegativeDutyCycle(int dutyCycle){
	TIM3->CCR2 = dutyCycle*amplitudeFactor;
}
void InitializeTimer4IT(){
	
	// Configure NVIC
	NVIC_InitTypeDef NVIC_InitStructure;
	// No StructInit call in API
	NVIC_InitStructure.NVIC_IRQChannel = TIM4_IRQn;
	NVIC_InitStructure.NVIC_IRQChannelSubPriority = 0;
	NVIC_InitStructure.NVIC_IRQChannelPreemptionPriority = 0;
	NVIC_InitStructure.NVIC_IRQChannelCmd = ENABLE;
	NVIC_Init(&NVIC_InitStructure);
	
	// Enable clock for timer 4
	RCC_APB1PeriphClockCmd(RCC_APB1Periph_TIM4 , ENABLE);
	// Create and initialize TimeBase structure
	TIM_TimeBaseInitTypeDef TIM_TimeBaseStructure;
	TIM_TimeBaseStructInit(&TIM_TimeBaseStructure);
	// Configure TimeBase structure
	TIM_TimeBaseStructure.TIM_Prescaler	= 0; // considering 72MHz, 1ms
	TIM_TimeBaseStructure.TIM_Period = 19999; // each 277,777777778 us
	TIM_TimeBaseStructure.TIM_CounterMode = TIM_CounterMode_Up;
	TIM_TimeBaseInit(TIM4, &TIM_TimeBaseStructure);
	
	// Enable interrupt and starting timer 4
	TIM_ITConfig(TIM4 , TIM_IT_Update , ENABLE);
	TIM_Cmd(TIM4 , ENABLE);
	
}

void InitializeGPIOInterruptionOnPB6(){
	// acording to https://scienceprog.com/interrupt-based-button-read-on-stm32f103zet6-board/
	// Interruption pin = PB1
	// Ext. Interruption Line = 0

	/* Enable clock for GPIOB */
	RCC_APB2PeriphClockCmd(RCC_APB2Periph_GPIOB, ENABLE);
	
	GPIO_InitTypeDef GPIO_InitStruct;
	EXTI_InitTypeDef EXTI_InitStruct;
	
	/* Set pin 6 as input Pull Down*/
	GPIO_InitStruct.GPIO_Pin = GPIO_Pin_1;
	GPIO_InitStruct.GPIO_Mode = GPIO_Mode_IPD;
	GPIO_InitStruct.GPIO_Speed = GPIO_Speed_2MHz;
	GPIO_Init(GPIOB, &GPIO_InitStruct);

	// Connect PB6 to External Interrupt Event Controller line 0
	RCC_APB2PeriphClockCmd(RCC_APB2Periph_AFIO, ENABLE);
	
	GPIO_EXTILineConfig(GPIO_PortSourceGPIOB, GPIO_PinSource1);
	
	
	//EXTI_StructInit(&EXTI_InitStruct);
	// PD1 is connected to EXTI_Line1 */
	EXTI_InitStruct.EXTI_Line = EXTI_Line1;
	EXTI_InitStruct.EXTI_Mode = EXTI_Mode_Interrupt;
	EXTI_InitStruct.EXTI_Trigger = EXTI_Trigger_Rising;
	EXTI_InitStruct.EXTI_LineCmd = ENABLE;
	EXTI_Init(&EXTI_InitStruct);
	
	RCC_APB2PeriphClockCmd(RCC_APB2Periph_AFIO, DISABLE);
	
	NVIC_InitTypeDef NVIC_InitStructure;
	NVIC_Init(&NVIC_InitStructure);
	//select NVIC channel to configure
	NVIC_InitStructure.NVIC_IRQChannel = EXTI1_IRQn;
	//set priority to lowest
	NVIC_InitStructure.NVIC_IRQChannelPreemptionPriority = 0x0F;
	//set subpriority to lowest
	NVIC_InitStructure.NVIC_IRQChannelSubPriority = 0x0F;
	//enable IRQ channel
	NVIC_InitStructure.NVIC_IRQChannelCmd = ENABLE;
	//update NVIC registers
	NVIC_Init(&NVIC_InitStructure);
	
	
	
	//NVIC_EnableIRQ(EXTI0_IRQn);
	
	
	
}

//EXTIn_IRQHandler - where n is the line which is also the pin
void EXTI1_IRQHandler(void){
	//Check if EXTI_Line0 is asserted
	if(EXTI_GetITStatus(EXTI_Line1) != RESET){
		toggle_led_PC13();
		
	}
	
	//we need to clear line pending bit manually
	EXTI_ClearITPendingBit(EXTI_Line1);
}

void TIM4_IRQHandler(void){
	// Update phases SPWMs
	updatePhaseR();
	updatePhaseS();
	updatePhaseT();
	// Update Interruption bit state
	TIM_ClearITPendingBit(TIM4 ,TIM_IT_Update);
}

void updatePhaseR(){
	if(t_senoid_R<60){
		changeRpositiveDutyCycle(senoid_pwm[t_senoid_R]);
		changeRnegativeDutyCycle(senoid_pwm[t_senoid_R]);
		t_senoid_R++;
	} else {
		t_senoid_R = 0;
		changeRpositiveDutyCycle(senoid_pwm[t_senoid_R]);
		changeRnegativeDutyCycle(senoid_pwm[t_senoid_R]);
	}
}

void updatePhaseS(){
	if(t_senoid_S<60){
		changeSpositiveDutyCycle(senoid_pwm[t_senoid_S]);
		changeSnegativeDutyCycle(senoid_pwm[t_senoid_S]);
		t_senoid_S++;
	} else {
		t_senoid_S = 0;
		changeSpositiveDutyCycle(senoid_pwm[t_senoid_S]);
		changeSnegativeDutyCycle(senoid_pwm[t_senoid_S]);
	}
}

void updatePhaseT(){
	if(t_senoid_T<60){
		changeTpositiveDutyCycle(senoid_pwm[t_senoid_T]);
		changeTnegativeDutyCycle(senoid_pwm[t_senoid_T]);
		t_senoid_T++;
	} else {
		t_senoid_T = 0;
		changeTpositiveDutyCycle(senoid_pwm[t_senoid_T]);
		changeTnegativeDutyCycle(senoid_pwm[t_senoid_T]);
	}
}


void toggle_led_PC13(){
	//toggle LED on pin PC13
		if(GPIO_ReadOutputDataBit(GPIOC, GPIO_Pin_13)){
			GPIO_ResetBits(GPIOC, GPIO_Pin_13);
		} else {
			GPIO_SetBits(GPIOC, GPIO_Pin_13);
		}

}

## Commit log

2019-06-28 attached interruption on timer 4
2019-06-28 attatched interrupt on timer 4 each 1ms
2019-07-05 added 3 phase pwm update functions
2019-07-09 added interruption on pin PB1
2019-07-09 adjusted interrupt timming to generate solid 60Hz SPWM
2019-07-14 implemented buttons (not phase control yet) and updated schematic
2019-07-15 added schematics
    [PCB.brd, PCB.sch]
2019-07-15 added protection diode on zero cross detector
    [PCB.brd, PCB.sch]
2019-07-18 finished PCB and corrected schematic
    [PCB.brd]
2019-07-18 added schematic pdf

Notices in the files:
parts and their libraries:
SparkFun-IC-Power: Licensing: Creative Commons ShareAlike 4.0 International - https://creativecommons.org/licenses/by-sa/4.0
